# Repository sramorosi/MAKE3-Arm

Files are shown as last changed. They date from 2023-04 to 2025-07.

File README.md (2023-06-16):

# MAKE3-Arm

This repository contains the complete design for the MAKE3 Robot Arm, controller, and the code to control the arm (both remote control and programmable).  This is intended to be a low-cost (less than US $ 250), do it yourself (mostly 3D printed or made with common shop tools), remote controlled robot arm. It can be used for stacking/unstacking things for fun, delivering things without getting too close, as a learning tool whereby you learn by making, and much more.

The design files are in the folder [OpenSCAD-code](/OpenSCAD-code) and are written in [OpenSCAD](https://openscad.org/).  This page contains the **Bill of Materials** for making the MAKE3 Robot Arm, along with notes about what drove the design.

The control code files are in the folder [MAKE3](/MAKE3) and are written in [Arduino C](https://www.arduino.cc/). This page contains information about how the code works and how to calibrate the code for your MAKE3 Robot Arm.
 
## MAKE3 Arm Assembly

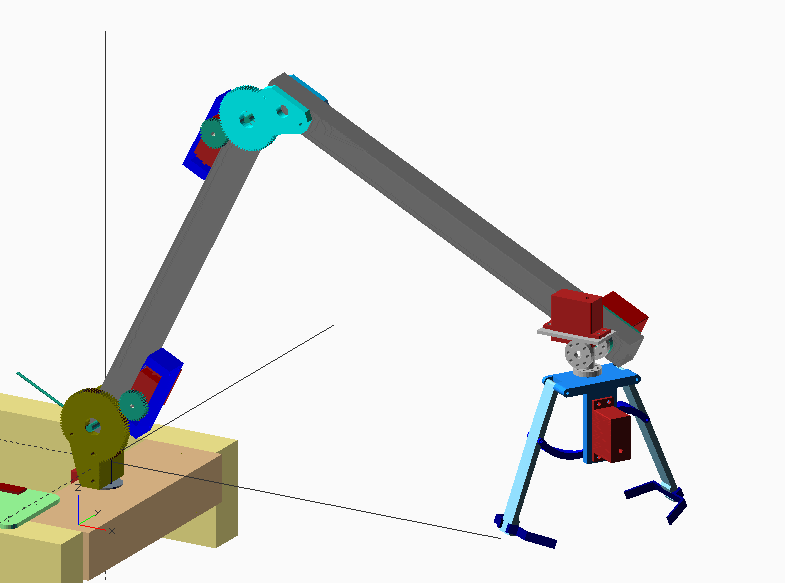
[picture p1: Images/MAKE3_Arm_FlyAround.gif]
MAKE3-Arm-gif

GIF animation of the MAKE3 Robot Arm created in OpenSCAD. 

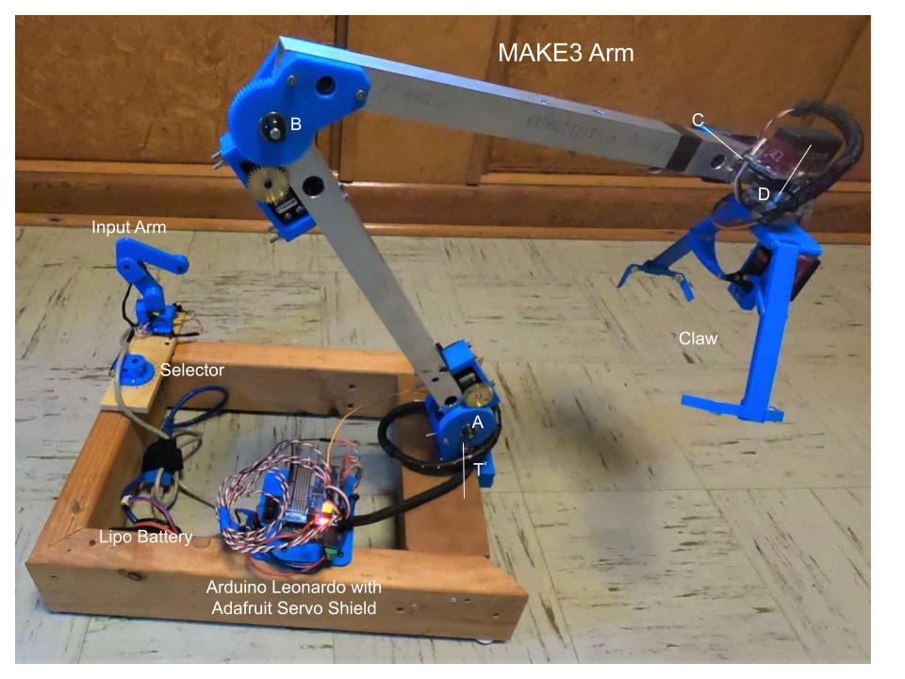
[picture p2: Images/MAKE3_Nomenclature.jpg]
MAKE3 Nomenclature

Labeled photo of the MAKE3 arm.

Video of the MAKE3 robot arm can be found [here](https://youtu.be/0xM0Xhr4jO0)

## MAKE3 Specification

1. The arm has a total reach of about 73 cm. The AB arm is 35 cm and the BC arm is 38 cm
1. The position accuracy at the claw is about plus or minus 0.7 cm. This is based on the angular accuracy of the servos times the gearing and the arm lengths
1. The arm can lift objects up to 200 grams
1. There are no sensors on the MAKE3

## Teaching Objectives

This project is intended as a low cost teaching tool to describe how to design, build and analyze a robot arm.  Some teaching objectives are:

1. Mechanical design of joints (strong, robust, accurate)
1. Principles of Statics (forces and torques/moments)
1. How to create smooth remote control motion
1. How to synchronize control of multiple servos
1. How to make programmed motions fast and smooth
1. How to use trigonometry to get arm angles from a desired point - Inverse Kinematics

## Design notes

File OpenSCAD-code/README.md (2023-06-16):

# OpenSCAD code for MAKE3-Arm

This folder contains the OpenSCAD files that define the MAKE3-Arm and Controllers.

Familiarity with OpenSCAD is required, to make the files for printing and to interogate the design.
 
The OpenSCAD design files are text files that contain the code for the designs.  Use these files to export the .stl files (STL or STereoLithography or Standard Triangle Language) for 3D printing. For more information on how to make .stl files see [making STL models from OpenSCAD](#making-stl-models-from-openscad)

The objective with MAKE3 was to make the design variable-driven (the variables are mostly at the top of each file and should work with the OpenSCAD **Customizer**).

Another objective was to perform some Engineering calculations on the design, using the variables, so one can quickly see if a design will work.

Another objective was to make the 3D printed parts not require supports when printing, to speed up the printing and make accurate parts (small, accurate, fast to print).

Note: OpenSCAD is a Functional Programming Language, and as such one cannot redefine a variable once it has been set.  Most of the code is "simple" programming but for computations involving arrays it becomes more complex.

MAKE3 Nomenclature
Labeled photo of the MAKE3 arm.

The next sections provide the **Bill of Materials** for the MAKE3 arm and control devices, organized by the OpenSCAD files. The files are divided into major assemblies, to keep the files from getting large. There are three major assembly files ([Claw Assembly](#claw_assemblyscad), [Controllers](#controllersscad), and the [MAKE3 Assembly](#make3_assyscad)) and a number of other `include` files that are used with these three main files (`use` is another type of included file in OpenSCAD).   Within the files, there are `modules` or `functions` that break up the code into sub-assemblies, details and other functions.

## MAKE3_Assy.scad

MAKE3-Arm-gif

GIF animation of the MAKE3 Robot Arm created in OpenSCAD. 
[See how to make gifs here](https://github.com/sramorosi/MAKE3-Arm/tree/main/OpenSCAD-code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)

Engineering calculations are performed to find the largest torque on the A, B and C servos.  From these torques a Margin of Safety (MS) calculation is performed to find out if the selected servo will work (that is have a positive MS).  These torques are echoed to the console window, as shown below, and will change as the variables are changed:

```
ECHO: LEN_AB = 350, LEN_BC = 380, LEN_CD = 160, PAYLOAD_MASS = 200
ECHO: BCweight = 259.774, ABweight = 336.371, " grams"
ECHO: "B SERVO MOTOR CAPABILITY=", 250000, " gram-mm"
ECHO: "B Big Gear teeth=", 70, " B_Small Gear teeth =", 32
ECHO: "B GEARED SERVO CAPABILITY=", BGeared_Max_Torque = 546875, " gram-mm"
ECHO: "A SERVO MOTOR CAPABILITY=", 250000, " gram-mm"
ECHO: "A Big Gear teeth=", 80, " ASmall Gear teeth =", 32
ECHO: "A GEARED SERVO CAPABILITY=", AGeared_Max_Torque = 625000, " gram-mm"
ECHO: "A OUTPUT ANGLE=", 144, " DEG"
ECHO: "Turtable Big Gear teeth=", 80, " Turntable Small Gear teeth =", 32
ECHO: "TURNTABLE OUTPUT ANGLE=", 144, " DEG"
ECHO: "C SERVO", " MARGIN OF SAFETY ", MS = 4.20833, max_load = 48000, pos = 4
ECHO: "B SERVO", " MARGIN OF SAFETY ", MS = 1.10963, max_load = 259228, pos = 4
ECHO: "A SERVO - NO SPRING", " MARGIN OF SAFETY ", MS = 0.138404, max_load = 549014, pos = 4
ECHO: A_spr_torque_min = -170310, A_spr_torque_max = 218970
ECHO: "A SERVO - SPRING", " MARGIN OF SAFETY ", MS = 0.797602, max_load = 347685, pos = 9
ECHO: "A SERVO - SPRING - NO PAYLOAD", " MARGIN OF SAFETY ", MS = 2.50475, max_load = -178329, pos = 20
```

The largest moments are *attempted* to be found by performing the calculations on a range of positions, using `function sweep1`. The largest moment values sometime show up at unusual positions. A **static** calculation is performed at each position.  No **dynamic** calculations are performed, and because of this one should have "large" static margins (MS values greater than 0.5 are recommended).

This design has a **torsion spring** located at joint A, which reduces the torque on the A servo.  Above, the fourth line from the bottom shows the margin without a spring (...NO SPRING ... MS = 0.13...) a small or negative MS is BAD.  With a spring MS = 0.79...  I have found that, with a MS less than 0.5, the servos tend to heat up quickly, damaging the servos (I have killed many servos along the way).

Here is the **Bill of Materials**:

### MAKE3_Assy - 3D printed

1. servo_mount (quantity 3), color blue
1. plain_guss (quantity 1), color DeepSkyBlue
1. B_gear_guss (quantity 1), color aqua
1. A_gear_lollypop (quantity 1), gear_side=true, color olive
1. A_gear_lollypop (quantity 1), gear_side=false, color olive
1. turntable_gear (quantity 1), color tomato
1. Electronics_Board (quantity 1), color palegreen

### MAKE3_Assy - Purchased Hardware or other

1. Claw Assembly - See [Claw_Assembly.scad](#claw_assemblyscad)
1. Tube for AB arm: 1" square x 0.065" thick Aluminum tube, 6061 or 6063. This tube is stiff torsionally and the wires can run inside of it. From Online Metals
1. Tube for BC arm: same material as AB arm 
1. Joint A:
    1. Servo, 360 degree, 35 kg-cm torque, FeeTech FT6335M-360, from Amazon
    2. Servo Gear, 32P, 32 Tooth, 25T 3F Spline Servo Mount Gear, from ServoCity
    4. Screws to attach servo to block, Phillips Rounded Head Thread-Forming Screws for Plastic, 18-8 Stainless Steel, Number 4 Size, 1/2" Long, from McMaster Carr
    5. Bearings for main shaft (quantity 2), FR4-ZZ 1/4" x 5/8" x 0.196" Flanged Radial Ball Bearing, from Amazon
    6. Axel, 1/4 inch bolt, or for better precision Rotary Shaft, 303 Stainless Steel, 1/4" Diameter, part no. 1257K115 from McMaster Carr
    1. Set Screw Shaft Collar for 1/4" Diameter (quantity 2), part no. 9414T6 from McMaster Carr 	
    7. Torsion Spring, 90 Degree Left-Hand Wound, 0.848" OD, 0.105" Wire Dia, part no. 9271K589 from McMaster Carr
1. Joint B, same as Joint A, except no spring
1. Joint C:
    1. Servo, 270 degree, 25 kg-cm torque, DS3225MG, from Amazon
    2. Servo Hub (25T Spline), from ServoCity
1. Joint D:
    1. Servo, 270 degree, 25 kg-cm torque, DS3225MG, from Amazon
    2. Standard Hub Shaft Servo Block (25T Spline), from ServoCity
1. Joint T (for turntable):
    1. Servo, 360 degree, 35 kg-cm torque, FeeTech FT6335M-360
    2. Servo Gear (25T Spline), 32 tooth, from ServoCity, same as above
    4. Screws to attach servo to block, same as above
    5. Two Flanged Hex Bore Precision Ball Bearings 1/2” Hex ID x 1-1/8” OD x 5/16” WD, for main shaft, from Amazon
    6. Main Shaft, 1/2" aluminum hex bar, 7075, from Online Metals
1. 2 by 4 wood for base

### MAKE3_Assy - Electronics

Here is the bill of material for the electronics (minus the servos and potentiometers, which are listed with the mechanical assemblies):

1. The microprocessor is an Arduino Leonardo (Note: an Arduino Uno does not work correctly with the Adafruit Servo Shield), from Amazon
1. Adafruit Servo Shield, Shield stacking headers for Arduino (R3 Compatible), 16-Channel 12-bit PWM/Servo Shield - I2C interface
1. Wires from controller to Arduino/Shield. The positive and ground wires can be common for all potentiometers). I have sacrificed CAT-5 Ethernet cable, which have four twisted pairs, or eight wires, so one can wire up to six potentiometers/switches along with the positive and ground wires. All 8 wires have unique colors, which makes it easy to keep track of the wires.
1. Battery - 7.4V Lipo, from Amazon
1. Rocker 2 Position ON-Off Toggle Switch AC 125V/20A, SPST 2 Pins, KCD3-101, from Amazon
1. Misc. connectors for the battery and switch

## Claw_Assembly.scad

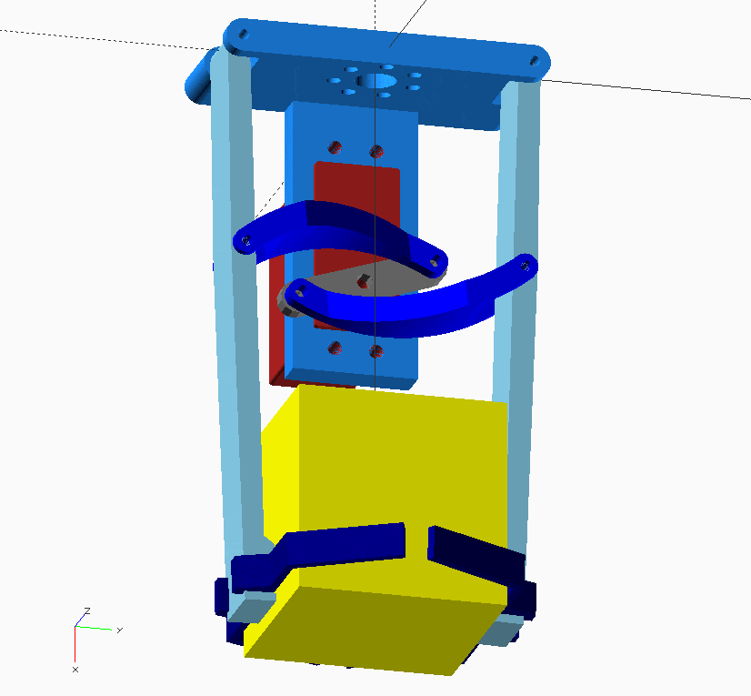
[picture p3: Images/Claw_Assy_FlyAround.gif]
Claw_Assy_FlyAround


This is the claw that attaches to the end of the robot arm. It is designed to be able to pick up items that are roughly 5 to 8 cm in size. The blue curved links are designed to lower the servo torque when the claw is closed, so the servo does not overheat when holding an object. The navy guides are designed to be clipped onto the claw_bars primarily so that 3D printing is faster.

### Claw Parts - 3D printed 

1. curved_link (quantity 2), color blue, supports required. Sometimes called "rod"
2. guide (quantity 2), color navy
3. claw_bar (quantity 2), color SkyBlue
4. base (quantity 1), color DodgerBlue

### Claw Parts - Purchased Parts

1. Servo, 180 degree, 25 kg-cm, DS3225MG, includes horn, horn screws, bushings, from Amazon
2. pins (quantity 4), Spring Steel Slotted Spring Pin, 5/64" Diameter, source McMaster Carr, part number 98296A149
3. screws (quantity 4), attach servo to base, same as for servos on Arm
4. foam window seal, to put on inside of guide for grip

## Controllers.scad

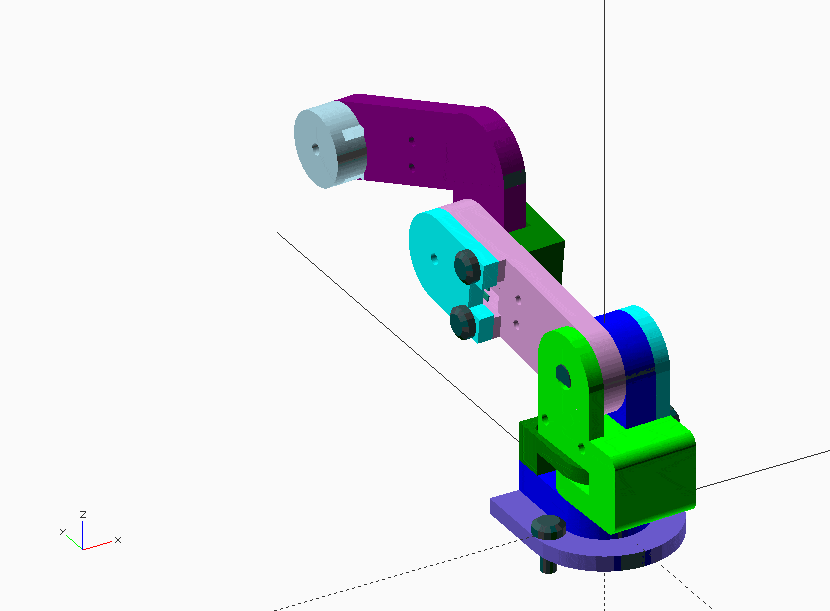
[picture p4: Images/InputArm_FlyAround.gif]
Controller_Arm


This is the *baby* robot arm used to control the big arm. The main design objective was to make the parts 3D printable without supports (for accuracy) so that when assembled the joints have just enough friction so that they move easily but the baby arm will also hold position when it is released.  This design accomplished that!

### Input Arm Controller Parts - 3D printed 

1. PotLug (quantity 2), color blue
2. NonPotLug (quantity 2), color green
3. PotCover (quantity 2), color cyan
4. BasePotCover (quantity 1), color SlateBlue
5. AB_Arm (quantity 1), color plum
6. BC_Arm (quantity 1), color purple
7. BC_Arm_Cap (quantity 1), color lightblue
8. TA_Fitting (quantity 1), color lime

### Input Arm Controller Parts - Purchased Parts

1. Potentiometer (quantity 3), P090L-03F20BR10K, from Mouser Electronics. Snip the extentions off (not the connectors), to fit in the input arm
1. Switch (quantity 1) 12x12x5mm Mini/Micro/Small PCB Momentary Tactile Tact Push Button Switch, from Amazon
1. Screws to hold things together (quantity 9), Phillips Rounded Head Thread-Forming Screws for Plastic, 18-8 Stainless Steel, Number 4 Size, 3/4" Long, from McMaster Carr

## Controllers.scad   (Selector Assembly controller shown)

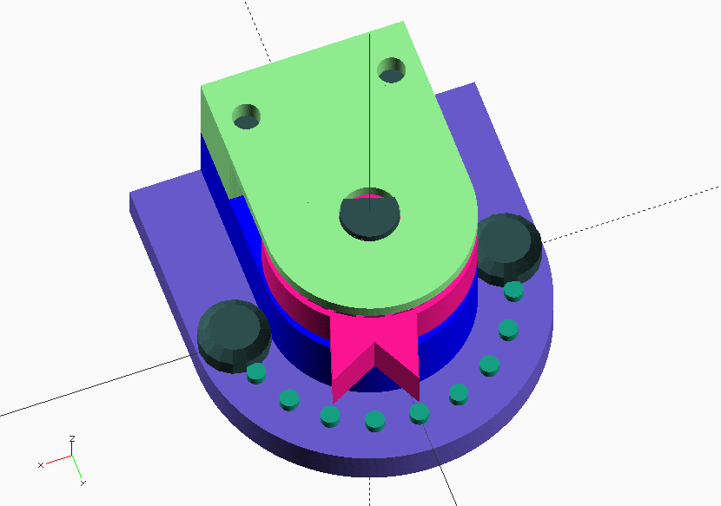
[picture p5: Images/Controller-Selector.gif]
Controller-Selector


### Selector Parts - 3D printed 

1. PotLug (quantity 1), color blue
2. NonPotLugTooth (quantity 1), color lightgreen
3. bumpyBaseCover (quantity 1), color plum
4. SelectorKnot (quantity 1), color DeepPink

### Selector Parts - Purchased Parts

1. Potentiometer (quantity 1), same as used in the input arm above

### Making STL models from OpenSCAD

To make STL models for 3D printing follow these steps for each part that you want to print. The OpenSCAD **Customizer** is handy for changing variables prior to exporting.
1. Toggle off the assembly.  Do not print assemblies.
```OpenSCAD
DISPLAY_ASSY = true;  // set this to false when exporting STL files
```
2. Adjust variables for printing, for example, set FACETS = 140. More facets makes the parts smoother, but takes longer to display.
```OpenSCAD
// use 140 for printing, 40 for display
FACETS = 100; // [40,140]
```
3. Toggle on and off the parts that you want to print by finding the line in the code that draws the part. Remove * (disable) prefix on the line.  Note:  These lines have // EXPORT AS STL at the end of the line.
```
*servo_mount(); // EXPORT AS STL, quantity 2.  remove the * for export
```
4. Render the part **(F6)** Note: Rendering can take much longer than Preview (F5), taking minutes rather than seconds.  Look for a progress bar on the lower right.
5. Export the rendered part as an STL file **(F7)**
6. Load the STL file into your favorite slicer.  Note: Occasionally you may need to perform some STL cleanup, when you detect something not working right in the slicer. I use the 3D Builder tool on Windows for STL repairs.

### Making Animation (.gif or video) files from OpenSCAD

The Animation function **Animate** in OpenSCAD can be toggled on under the **View** menu.

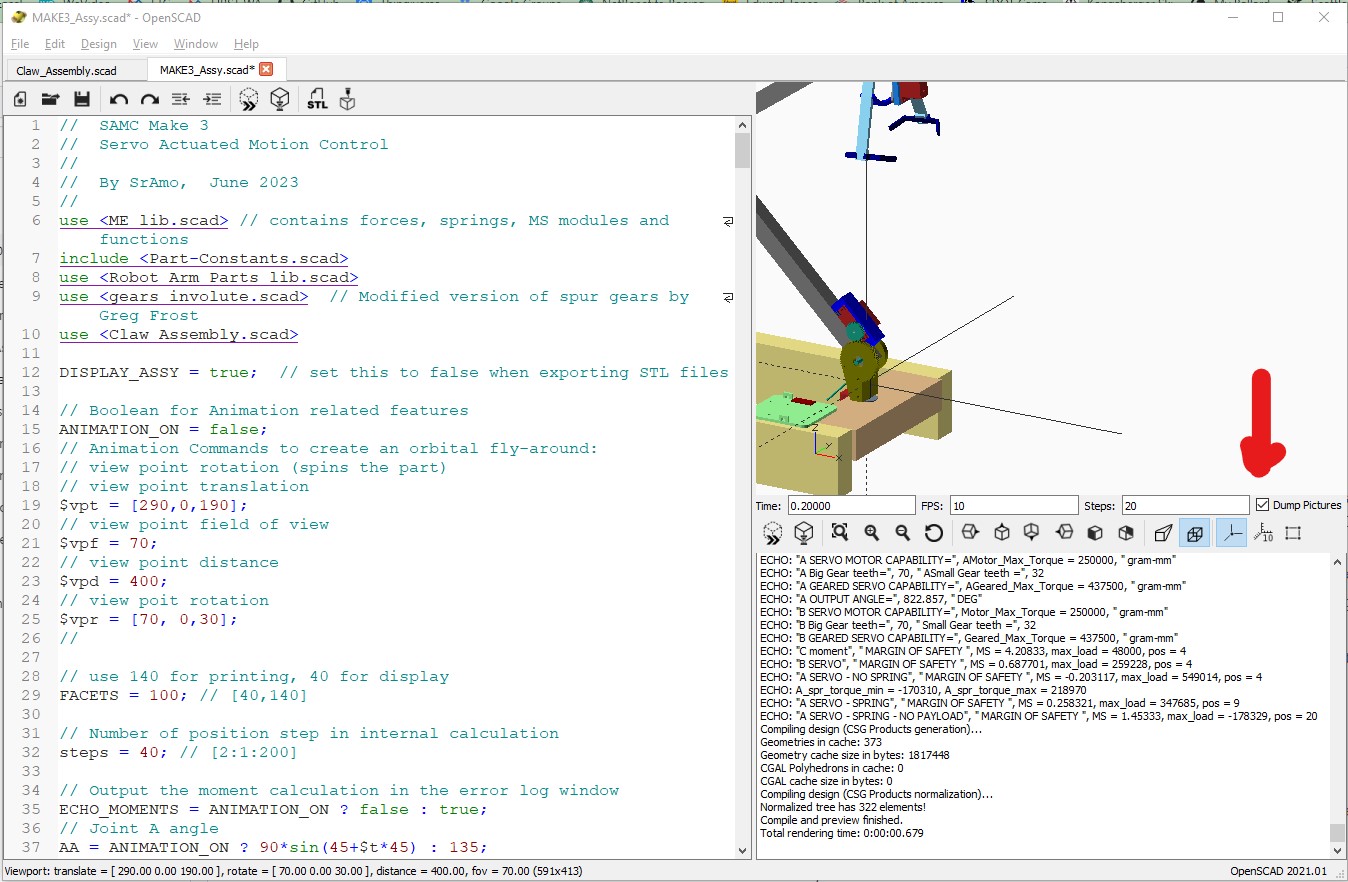
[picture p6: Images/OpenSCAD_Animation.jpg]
MAKE3 Animation Example


While **Animate** is running, enter numbers for FPS and Steps, and check the "Dump Pictures" box just above the console window.  One picture will be created for each frame and saved in the same folder as your OpenSCAD file.

Use the free tool at EZGIF.COM [here](https://ezgif.com/maker) to make a gif or video.  Upload all of the dumped pictures and follow the steps for making a gif.

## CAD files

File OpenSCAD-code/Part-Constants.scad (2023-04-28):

// PART CONSTANT Configuration File
//  last modified October 5 2021 by SrAmo

// conversions
mm_inch = 1/25.4;

// 1/4 ID bearing OD if using a bearing (PART FR4-ZZ C3)
Qtr_bearing_id = 0.25/mm_inch;
Qtr_bearing_od=0.628/mm_inch; // 0.628 inch = 15.9512 mm
Qtr_bearing_flange_od=0.71/mm_inch; // .71 inch = 18.034 mm
Qtr_bearing_flange_t=0.05/mm_inch; // 0.05 inch = 1.27 mm
Qtr_bearing_t=0.155/mm_inch; // 0.155 inch = 3.937 mm

// 1/2 ID flanged bearing 
Half_bearing_id=0.50/mm_inch;
Half_bearing_od=1.125/mm_inch;
Half_bearing_flange_od=1.23/mm_inch; 
Half_bearing_flange_t=0.06/mm_inch; 
Half_bearing_t=0.31/mm_inch; 

M6_bearing_od=12; 
M6_bearing_flange_od=13.6;
M6_bearing_flange_t=0.8;
M6_bearing_t=3.15;

// round belt diameter throughout, if used
//belt_d=4.826;   // 0.19 in = 4.826 mm

hole_qtr_inch=6.48;   // hole for 0.25 inch joint/bolt 0.255 inch = 6.477 mm
hole_no6_screw = 2.5; // hole start diameter for number 6 screw 0.095 inch = 2.413
hole_M3=3.1; // hole for M3 (3 mm) joint/bolt
//hole_M5=5.1;  
hole_M6=6.1;
hole_servo_bushing=3.81; // hole for servo bushing 0.15 inch = 3.81 mm

// STANDARD 40MM X 20MM X 40MM SERVO DIMENSIONS
svo_l = 40.66; // Servo Length for openings in parts
svo_w = 20.3; // Servo Width for openings in parts
svo_d = 42; // Servo Depth from Horn interface to bottom of part
svo_shaft = 10.6; // Servo dist from shaft to edge of body in length direction, was 10.2
svo_screw_l = 49.5; // Servo screw hole length between
svo_screw_w = 10; // Servo screw hole width between
svo_flange_l = 57; // Servo flange length, was 55
svo_flange_t = 3; // Servo flange thickness
svo_flange_d = 10; // Servo depth from Horn interface to top of flange
servo_horn_l=25;
servo_horn_d1=15.25;
servo_horn_d2=7.5;
servo_horn_t=7.4;

// Springs
//  McMaster Carr 9271K619, torsion spring, used in MAKE 2
9271K619_angle = 180; // free leg angle
9271K619_OD = 19.35; // mm
9271K619_wd = 1.9;  // wire diameter mm
9271K619_len = 51;  // arm length mm
9271K619_coils = 7;  // number of coils
9271K619_LH = true;  // LH or RH (false)
9271K619_t = (9271K619_coils+1)*9271K619_wd; // thickness of the spring
9271K619_ID = 9271K619_OD-2*9271K619_wd;  // ID of the coil

//  McMaster Carr 9271K589, torsion spring, used in MAKE 3
9271K589_angle = 90; // free leg angle
9271K589_OD = 21.54; // mm
9271K589_wd = 2.667;  // wire diameter mm
9271K589_len = 88.9;  // arm length mm
9271K589_coils = 5.25;  // number of coils
9271K589_LH = true;  // LH or RH (false)
9271K589_t = (9271K589_coils+1)*9271K589_wd; // thickness of the spring
9271K589_ID = 9271K589_OD-2*9271K589_wd;  // ID of the coil
//9271K589_Dshaft = 12.7; // The largest shaft that can go through spring

pot_shaft_dia = 6.2; // mm, potentiometer shaft dia
pot_lug_t = 8; // thickness of the lug over potentiometer shaft

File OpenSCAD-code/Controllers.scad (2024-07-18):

// Input Control Arm Assembly and Selector Control assembly
//  Design for Human Hand to control a Robot Arm
//  last modified May 2023 by SrAmo
// The parts are designed to not require support material when 3D printing.
//
//  To make STL models for 3D printing follow these steps:
//  find "Export as STL" and remove the * (disable) suffix, 
//     then render the part (F6) (this may take some time)
//        then  Export as STL (F7)
use <ME_lib.scad> // contains forces, springs, MS modules and functions
include <Part-Constants.scad>
use <Robot_Arm_Parts_lib.scad>

/* Animation Commands to create an orbital fly-around:
$vpr = [60, 0, -30];   // view point rotation (spins the part)
$vpt = [-50,0,70];    // view point translation
$vpf = 50;          // view point field of view
$vpd = 150;         // view point distance
*/

// Parameters for Customizer:
// Joint A angle
//AA = 25; // [0:180.0]
AA = 100; //-90*sin($t*180);  // for animation
// Joint B angle
//BB = -35; // [-170:1:0.0]
BB = -50; //90*sin($t*180);  // for animation
// Turntable angle
//TT = 0; // [-90:90]
TT = 60*sin($t*90);  // for animation
// use 140 for printing, 40 for display
FACETS = 100; // [40,140]

// Draw the Input Arm Assembly?
display_assy = true;
// Draw the Selector?
display_selector = false;
// Section cut Assy at X = 0?
clip_yz = false;
// Section cut Assy at Z = 0?
clip_xy = false;

// length of full size A-B arm (mm)
LEN_AB_LARGE=350; 
// length of full size B-C arm (mm)
LEN_BC_LARGE=380; 

// For the Big Arm to move the same as the Small Arm
//  the link lengths should be of consistent scale.
SCALE = 0.15;  // scale of small to big arm

// length of A-B arm, color = plum
lenAB=SCALE*LEN_AB_LARGE;     // mm
// length of B-C arm, color = blue
lenBC=SCALE*LEN_BC_LARGE;      // mm
echo("Baby Arm lengths",SCALE=SCALE,lenAB=lenAB,lenBC=lenBC," mm");

// A joint shift Z (up), mm
A_joint_Z = 34; 
// A joint shift X (lateral), mm
A_joint_X = -9;

// Lug Diameter, mm, used by many
LUG_DIA = 22; 
// distance to the flat side from the bore
FLAT_DIST = 16;
// Main Lug Thickness, mm
MAIN_LUG_THK = 6;
OUTER_LUG_THK = 4;
POT_LUG_THK = 8;
// LUG_Z is the offset for pot removal
LUG_Z = 2;

// Slip fit hole for potentiometer shaft
POT_HOLE_DIA = 6.3; // mm
// McMaster Carr Screw No. 90380A274  to hold lugs together (quantity about 10)
SCREW_DIA = 3.3; // mm, For no. 4 plastic screw, length 0.75 inch

zbody = 5.5;  // Offset for potentiometer body, all units are mm

module screwHoles(dia=15,shrink=false) { // pair of screw holes that hold the stack together
    cylDia = shrink ? SCREW_DIA*0.76 : SCREW_DIA;
    translate([dia/2.8,-dia/2-1,0]) 
        cylinder(h=4*dia,d=cylDia,center=true,$fn=FACETS);
    translate([-dia/2.8,-dia/2-1,0]) 
        cylinder(h=4*dia,d=cylDia,center=true,$fn=FACETS);
}
*rotate([0,0,180]) screwHoles(dia=LUG_DIA);

module ScrewsInHoles(lug_dia=15,screw_dia=4,screw_len=10) { // pair of screws
    // Rounded Head Thread-Forming Screws for Plastic
    translate([lug_dia/2.8,-lug_dia/2-1,0])  Screw(length=screw_len,dia=screw_dia);
    translate([-lug_dia/2.8,-lug_dia/2-1,0]) Screw(length=screw_len,dia=screw_dia);
}

// Full round top, width = dia
module roundTopLug (dia=15,hgt=20,thk=5,bore=3,cyl=false) {  
    difference() {
            hull() {
                translate([0,0,thk/2]) cylinder(h=thk,d=dia,center=true);
                translate([0,-hgt*3/4,thk/2]) cube([dia,hgt/2,thk],center=true);
            }
        cylinder(h=4*thk,d=bore,center=true);  // remove bore
            
        if(cyl) {    
            translate([dia/1.9,-dia/3.1,0]) 
                cylinder(h=hgt*2,d=dia/3.2,center=true,$fn=FACETS);
            translate([-dia/1.9,-dia/3.1,0]) 
                cylinder(h=hgt*2,d=dia/3.2,center=true,$fn=FACETS);
        }
            
    }
}
*roundTopLug(dia=LUG_DIA,hgt=FLAT_DIST,thk=OUTER_LUG_THK,bore=3,$fn=FACETS);  // note result if hgt < dia/2
*roundTopLug(dia=LUG_DIA,hgt=FLAT_DIST,thk=OUTER_LUG_THK,bore=3,cyl=false,$fn=FACETS);

module roundTopLugTwo (width=20,rad=2,hgt=8,thk=5,bore=3) { // Two radius round top
    cylWidth = width/2 - rad;
    difference() {
        translate([0,0,thk/2])
            hull() {
                translate([cylWidth,0,0]) cylinder(h=thk,r=rad,center=true);
                translate([-cylWidth,0,0]) cylinder(h=thk,r=rad,center=true);
                translate([0,-hgt/2,0]) cube([width,hgt,thk],center=true);
            }
        cylinder(h=4*thk,d=bore,center=true);  // remove bore
    }
}
*roundTopLugTwo(bore=0,$fn=FACETS);  // note result if hgt < dia/2

module PotLug(dia=LUG_DIA) {  // Model of Potentiometer holder
    color("blue") difference () {// Side that holds the POT
        roundTopLug(dia=dia,hgt=FLAT_DIST,thk=POT_LUG_THK,bore=POT_HOLE_DIA,$fn=FACETS);

        translate([0,0,zbody]) P090L_pot(negative=true);// remove potentiometer interface

        screwHoles(dia=LUG_DIA);  // remove screw holes
        }
}
*rotate([0,180,0]) PotLug(); // Export as STL... F7 (quantity 2)

module NonPotLug(thk=OUTER_LUG_THK) {  // Model of Potentiometer holder
    color("green") difference() {
            union() {
            translate([0,0,MAIN_LUG_THK]) 
                roundTopLug(dia=LUG_DIA,hgt=FLAT_DIST,thk=thk,bore=POT_HOLE_DIA,$fn=FACETS);
            translate([-LUG_DIA/2,-FLAT_DIST,0]) 
                cube([LUG_DIA,8.5,MAIN_LUG_THK],center=false);
        }
        // remove screw holes
        screwHoles(dia=LUG_DIA,shrink=true);
        
        // remove lug arc from cube
        translate([0,0,-.2]) 
            cylinder(h=MAIN_LUG_THK+.4,d=LUG_DIA*1.03,center=false,$fn=FACETS);
        
        // remove spring wave washer dish
        cylinder(h=MAIN_LUG_THK+.6,d=9.1,center=false,$fn=FACETS);
        
        // remove corner for BC arm motion
        translate([LUG_DIA/2,-LUG_DIA/2,-.2]) rotate([0,0,45])
            cube([6,6,MAIN_LUG_THK+.4],center=false);
    }
}
*rotate([0,180,0]) NonPotLug(); // Export as STL... F7 (quantity 2)

module PotCover() {
    color("cyan") 
    difference () {// Side that holds the POT
        rotate([0,180,0]) 
            translate([0,0,-OUTER_LUG_THK]) 
                roundTopLug(dia=LUG_DIA,hgt=FLAT_DIST,thk=OUTER_LUG_THK,bore=3,cyl=false,$fn=FACETS);
        // Above was cyl=true and trans and rot not required
        // remove potentiometer interface
        translate([0,0,OUTER_LUG_THK+zbody]) P090L_pot(negative=false);
        screwHoles(dia=LUG_DIA);  // remove screw holes
        translate([0,-FLAT_DIST+2,0]) cube([LUG_DIA/2.6,10,10],center=true);
    }
}
*PotCover(); // Export as STL... F7 (quantity 2)

module PotCoverAssy() {
    PotCover();
    ScrewsInHoles(lug_dia=LUG_DIA,screw_dia=4,screw_len=19);
}
*PotCoverAssy();


module joint_visuals(cut=true) { // Use for cross section cuts of Joints
    difference() { 
        union() {
            PotLug(); 
            translate([0,0,zbody]) P090L_pot(negative=false); 
            translate([0,0,POT_LUG_THK]) NonPotLug(); // OR SELECTOR BASE
            translate([0,0,-OUTER_LUG_THK]) PotCoverAssy();
            rotate([0,0,90]) 
                translate([0,0,MAIN_LUG_THK+.2]) 
                    scale([.95,.95,.95]) 
                        AB_Arm(len = lenAB);
       }
       if (cut) translate([-20,0,0]) cube([40,80,40],center=true);  // Section Cut cube
    }
}
*joint_visuals(cut=true); // not for print

module zip_holes() {
    translate([0,3.5,0]) cylinder(h=20,d=2.5,center=true,$fn=36);
    translate([0,-3.5,0]) cylinder(h=20,d=2.5,center=true,$fn=36);
}

module AB_Arm(len=100) {
    color("plum",1) difference () {
        union() {
            translate([0,0,8]) 
                rotate([180,0,-90]) 
                difference() {
                    roundTopLug(dia=LUG_DIA,hgt=FLAT_DIST,thk=MAIN_LUG_THK, bore=3, cyl=true,$fn=FACETS);
                // remove potentiometer interface
                translate([0,0,-LUG_Z]) scale([1.02,1.02,1.02]) rotate([0,0,180]) 
                    P090L_pot(negative=true);
            }
            
            translate([len,0,-0]) 
                rotate([0,0,-90]) PotLug(); // lug at other end
            
            // The connecting cube:
            difference() { // REMOVE CYL SO THAT 0,0 LUG JOINT UNIONS PROPERLY
                translate([LUG_DIA/1.8,-LUG_DIA/2,LUG_Z]) 
                    cube([len-LUG_DIA/.8,LUG_DIA,MAIN_LUG_THK],center=false);
                cylinder(h=40,d=8,center=true,$fn=FACETS); // for the pot
                translate([len/2.6,0,0]) zip_holes();
           }
        }
    }
}
*rotate([180,0,0]) AB_Arm(len = lenAB); // Export as STL... F7 (quantity 1)

module AB_Arm_Assy(len=100){
    AB_Arm(len=len); 
    translate([len,0,0])  rotate([0,0,-90]) {
        translate([0,0,-OUTER_LUG_THK])PotCoverAssy();
        translate([0,0,POT_LUG_THK]) NonPotLug();
    }
    translate([lenAB,0,5]) rotate([0,0,-90]) P090L_pot(negative=false);
}
*AB_Arm_Assy(len=lenAB);
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

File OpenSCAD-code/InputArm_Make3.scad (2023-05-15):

// Input Arm Assembly
//  Design for Human Hand to control a Robot Arm
//  last modified May 2023 by SrAmo
// The parts are designed to not require support material when 3D printing.
//
//  To make STL models for 3D printing follow these steps:
//  find "Export as STL" and remove the * (disable) suffix, 
//     then render the part (F6) (this may take some time)
//        then  Export as STL (F7)
use <ME_lib.scad> // contains forces, springs, MS modules and functions

// Animation Commands to create an orbital fly-around:
$vpr = [60, 0, -30];   // view point rotation (spins the part)
$vpt = [-40,0,80];    // view point translation
$vpf = 50;          // view point field of view
$vpd = 180;         // view point distance
//

// Parameters for Customizer:
// Joint A angle
//AA = 25; // [0:180.0]
AA = 90*sin($t*180);  // for animation
// Joint B angle
//BB = -35; // [-170:1:0.0]
BB = -80*sin($t*90);  // for animation
// Turntable angle
//TT = 0; // [-90:90]
TT = 60*sin($t*90);  // for animation
// use 140 for printing, 40 for display
FACETS = 40; // [40,140]

// Draw the Input Arm Assembly?
display_assy = true;
// Draw the Selector?
display_selector = true;
// Section cut Assy at X = 0?
clip_yz = false;
// Section cut Assy at Z = 0?
clip_xy = false;

// length of full size A-B arm (mm)
LEN_AB_LARGE=350; 
// length of full size B-C arm (mm)
LEN_BC_LARGE=380; 

// For the Big Arm to move the same as the Small Arm
//  the link lengths should be of consistent scale.
SCALE = 0.15;  // scale of small to big arm

// length of A-B arm, color = plum
lenAB=SCALE*LEN_AB_LARGE;     // mm
// length of B-C arm, color = blue
lenBC=SCALE*LEN_BC_LARGE;      // mm
echo("Baby Arm lengths",SCALE=SCALE,lenAB=lenAB,lenBC=lenBC," mm");

// A joint shift Z (up), mm
A_joint_Z = 40; 
// A joint shift X (lateral), mm
A_joint_X = -9;

// Lug Diameter, mm, used by many
LUG_DIA = 22; 
// distance to the flat side from the bore
FLAT_DIST = 20;
// Main Lug Thickness, mm
MAIN_LUG_THK = 6;
OUTER_LUG_THK = 4;
POT_LUG_THK = 8;
// LUG_Z is the offset for pot removal
LUG_Z = 2;

// Slip fit hole for potentiometer shaft
POT_HOLE_DIA = 6.3; // mm
// McMaster Carr Screw No. 90380A274  to hold lugs together (quantity about 10)
SCREW_DIA = 3.3; // mm, For no. 4 plastic screw, length 0.75 inch

//################### PART LIB FUNCTIONS AND MODULES
module washer(d=20,t=2,d_pin=10,center=true){
    // model washer on xy plane at 0,0,0 of diameter d, hole size of d_pin
    // t is thickness
    difference(){
        cylinder(t,d=d,center=center);  // outside
        cylinder(3*t,d=d_pin,center=true);  // subtract bore
    };
}
*washer($fn=FACETS); 

module rounded_cube(size=[20,30,10],r=5,center=true) {
    // Create a rounded cube in the xy plane, flat on the Z ends
    // Creates 4 cylinders and then uses hull
    
    xp=center ? size[0]/2-r : size[0]-r;
    yp=center ? size[1]/2-r : size[1]-r;
    xn=center ? -xp : r;
    yn=center ? -yp : r;
    z=center ? 0 : size[2]/2;

    hull() {
        translate([xp,yp,z]) cylinder(h=size[2],r=r,center=true);
        translate([xp,yn,z]) cylinder(h=size[2],r=r,center=true);
        translate([xn,yp,z]) cylinder(h=size[2],r=r,center=true);
        translate([xn,yn,z]) cylinder(h=size[2],r=r,center=true);       
    }  
}
*rounded_cube(center=false,$fn=FACETS); 

L_pot_shaft = 13.1;  // P090 shaft length above the body (mm)
zbody = 5.5;  // all units are mm

module P090L_pot (negative=false) {
// The P090L (Style L) has the three pins off of the side
// Digi-key part no. P090S-04F20BR10K or P090S-14T20BR10K
// https://www.digikey.com/en/products/detail/tt-electronics-bi/P090S-04F20BR10K/2408853 
// https://www.mouser.com/ProductDetail/BI-Technologies-TT-Electronics/P090S-14T20BR10K
// Solder the wires to the pins (need solid connection). Pins can be easily bent.
// Cut off connectors to reduce installation volume with small diagonal cutters.
// negative false = model a potentiometer for display
// negative true = model to be used with a difference() in another model
    
    ss = negative ? 1.0: 0.97;  // if negative == false then scale down
    // constants
    zbDif = zbody+1;  // make body bigger for difference()

    scale([ss,ss,ss]){ // scale down the model for display
        color("green") if (!negative) { // potentiometer for display
            translate([0,0,-zbody/2]) cube([10,12,zbody],center=true);
            // two cylinders on backside, drawn larger than real
            translate([0,-8.5/2,-zbody]) cylinder(h=4,d=3,center=true,$fn=FACETS);
            translate([0,8.5/2,-zbody]) cylinder(h=4,d=3,center=true,$fn=FACETS);

        } else {         // potentiometer for difference()
            translate([0,0,-zbDif/2]) cube([10,12.5,zbDif],center=true);
            translate([0,-12.5,-zbDif/2]) cube([10,20,zbDif],center=true);
        }
        
        cylinder(h=2,d=7.2,center=true,$fn=FACETS); // ring around the shaft
        
        // two cylinders around the shaft
        translate([2.7,-3.8,0]) cylinder(h=2,d=3,center=true,$fn=FACETS);
        translate([-2.7,3.8,0]) cylinder(h=2,d=3,center=true,$fn=FACETS);
        
    
        // shaft F-Type
        color("darkslategrey") 
            difference () {
                translate([0,0,L_pot_shaft/2]) 
                    cylinder(h=L_pot_shaft,d=6.2,center=true,$fn=FACETS);
                // 1.55 was 1.45, increased to make assembly easier
                translate ([-5,-L_pot_shaft-1.55,5]) cube(L_pot_shaft,center=false); // key
        }
        // pins (3)
        zpin = -4;
        translate([0,-11,zpin]) elect_pin();
        translate([-3,-11,zpin]) elect_pin();
        translate([3,-11,zpin]) elect_pin();
    }
     
    module elect_pin() { // 1 mm diamater electric pin
        cube([1.5,10,0.5],center=true);
    }
}
*P090L_pot(negative=false); 

//######################################################## //
module screwHoles(dia=15,shrink=false) { // pair of screw holes that hold the stack together
    cylDia = shrink ? SCREW_DIA*0.9 : SCREW_DIA;
    translate([dia/2.8,-dia/2-4,0])  cylinder(h=4*dia,d=cylDia,center=true,$fn=FACETS);
    translate([-dia/2.8,-dia/2-4,0]) cylinder(h=4*dia,d=cylDia,center=true,$fn=FACETS);
}
module roundTopLug (dia=15,hgt=20,thk=5,bore=3) {  // Full round top, width = dia
    difference() {
        translate([0,0,thk/2])
            hull() {
                cylinder(h=thk,d=dia,center=true);
                translate([0,-hgt/2,0]) cube([dia,hgt,thk],center=true);
            }
        cylinder(h=4*thk,d=bore,center=true);  // remove bore
    }
}
*roundTopLug(dia=20,hgt=5,bore=0,$fn=FACETS);  // note result if hgt < dia/2

module roundTopLugTwo (width=20,rad=2,hgt=8,thk=5,bore=3) { // Two radius round top
    cylWidth = width/2 - rad;
    difference() {
        translate([0,0,thk/2])
            hull() {
                translate([cylWidth,0,0]) cylinder(h=thk,r=rad,center=true);
                translate([-cylWidth,0,0]) cylinder(h=thk,r=rad,center=true);
                translate([0,-hgt/2,0]) cube([width,hgt,thk],center=true);
            }
        cylinder(h=4*thk,d=bore,center=true);  // remove bore
    }
}
*roundTopLugTwo(bore=0,$fn=FACETS);  // note result if hgt < dia/2

module PotLug() {  // Model of Potentiometer holder
    color("blue") difference () {// Side that holds the POT
        roundTopLug(dia=LUG_DIA,hgt=FLAT_DIST,thk=POT_LUG_THK,bore=POT_HOLE_DIA,$fn=FACETS);

        translate([0,0,zbody]) P090L_pot(negative=true);// remove potentiometer interface

        screwHoles(dia=LUG_DIA);  // remove screw holes
        }
}
*rotate([0,180,0]) PotLug(); // Export as STL... F7 (quantity 4)

module NonPotLug(thk=OUTER_LUG_THK,notch=false) {  // Model of Potentiometer holder
    color("green") difference() {
            union() {
            translate([0,0,MAIN_LUG_THK]) 
                roundTopLug(dia=LUG_DIA,hgt=FLAT_DIST,thk=thk,bore=POT_HOLE_DIA,$fn=FACETS);
            translate([-LUG_DIA/2,-FLAT_DIST,0]) cube([LUG_DIA,8.5,MAIN_LUG_THK],center=false);
            if (notch) translate([0,LUG_DIA/2.2,MAIN_LUG_THK]) rotate([90,0,0])
            linear_extrude(3,convexity=10) polygon(points=[[1.5,0],[0,-1.2],[-1.5,0]]);
        }
        // remove screw holes
        screwHoles(dia=LUG_DIA,shrink=true);
    }
}
*NonPotLug();

module PotCover() {
    color("Cyan") 
    difference () {// Side that holds the POT
        roundTopLug(dia=LUG_DIA,hgt=FLAT_DIST,thk=OUTER_LUG_THK,bore=3,$fn=FACETS);
        // remove potentiometer interface
        translate([0,0,OUTER_LUG_THK+zbody]) P090L_pot(negative=false);
        screwHoles(dia=LUG_DIA);  // remove screw holes
        translate([0,-FLAT_DIST,0]) cube([LUG_DIA/2.6,10,10],center=true);
    }
}
*PotCover(); // STL (2)
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

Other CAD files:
OpenSCAD-code/Robot_Arm_Parts_lib.scad
OpenSCAD-code/Claw_Assembly.scad
OpenSCAD-code/MAKE3_Assy.scad
OpenSCAD-code/ME_lib.scad
OpenSCAD-code/gears_involute.scad

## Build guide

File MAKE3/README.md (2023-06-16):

# Robot Arm Control Code for MAKE3-Arm

This folder contains the Arduino Robot Arm control software for the MAKE3-Arm.

It is written in the C programming language (it does not use C++ objects).  Variables have been grouped into structures using `struct`, to help organize the code.

An understanding of how microcontrollers work is required. Specifically there is an initialization function `setup()` and a repeating `loop()` function. For good robot arm performance it is important to let `loop()` loop as fast as possible. Slow loops can make the arm response jerky and potentially introduce unsteady dynamics. For reference, the MAKE3 runs about 14 milliseconds/loop while in remote control, and about 9 milliseconds/loop while in programmed mode.

The MAKE3 Robot Arm is driven by servos. Servos take **position** command as their input. With the MAKE3, the servo commands are being given (written) every loop!

## Top Level Operation of MAKE3 Arm

There are two basic ways to control the arm. The first is by **remote control** (also called TELEOPERATED), which is the easiest to get working. The second is 
**programmed mode** (also called AUTONOMOUS), which takes more coding and is described further down.

The code is written to control the main arm using the control **Input Arm** and the **Selector**. See folder [OpenSCAD-code](/OpenSCAD-code) for the design of these two control devices.   To avoid using the Selector (recommended for first setup), **add a jumper between analog I/O port 8 and Ground**. This tells the code to stay in TELEOPERATED mode.

The **Input Arm** (or baby arm) is scaled down version of the MAKE3 arm, but it only has joints A, B and T (turntable); it only has potentiometers for these three joints.  The Input Arm also has a **button to control the Claw**, which toggles the claw open and closed.

### Wrist Servos, C and D

The wrist servos, C and D, are always controlled by code (not by an input potentiometer).  In general, the code makes the C servo always point straight down (-90 degrees in global C angle sence). This is done by the function `getCang` shown below.  D is likewise made to **aim** the Claw in a global angle sence. 

```c++
float getCang(float a_angle, float b_angle, float fixed_c_angle) { // returns joint angle C, using A and B
  // Assumes that you want an absolute (fixed) C angle
  return -a_angle - b_angle + fixed_c_angle;
}
```

Having C and D controlled by code makes the arm much easier to operate.

## Calibration of your MAKE3 Arm 

Once a new MAKE3 Robot Arm is completely built, the **first step** is to determine constants for Potentiometers and Servos. These are set in the `setup()` function.
I recommend using a servo tester to get the initial range of motion correct before hooking the servos up the the Arduino/Shield. The calibration involves mapping physical potentiometer angles to millivolt readings and servo angles to microsecond (PWM pulse width) readings.

```c++
void setup() {  // setup code here, to run once:
  // TUNE POTENTIOMETER LOW AND HIGH VALUES
  // FORMAT: initPot(pin,lowmv,lowang,highmv,highang)
  make3.jA.pot = initPot(1 ,905,  0/RADIAN, 112, 180/RADIAN); 
  make3.jB.pot = initPot(5 ,500,-90/RADIAN, 908,  0/RADIAN); 
  make3.jT.pot = initPot(0 ,894, 90/RADIAN, 127, -90.0/RADIAN); 
  jS.pot = initPot(2 , 0, 0/RADIAN, 1023, 280/RADIAN); 

  // TUNE SERVO LOW AND HIGH VALUES
  // FORMAT: initServo(pin,lowang,lowms,highang,highms)
  make3.jA.svo = initServo(0,  7.0/RADIAN, 505, 90.0/RADIAN, 1551);
  make3.jB.svo = initServo(1, 0.0/RADIAN, 500,-175.0/RADIAN, 2320);
  make3.jC.svo = initServo(2, -90.0/RADIAN, 927, 0.0/RADIAN, 1410);
  make3.jD.svo = initServo(3,  -90.0/RADIAN,  811, 90.0/RADIAN, 2054); 
  make3.jCLAW.svo = initServo(4, -45.0/RADIAN,  500, 45.0/RADIAN, 2000); 
  make3.jT.svo = initServo(5,  70.0/RADIAN,  2347, -70.0/RADIAN, 465); 

```

At the end of the main loop there are some telemetry functions (that write values to Serial Output) to help with the callibration:

```c++
  //  Serial Output for Initial Calibration.  One line for each servo.  Turn on one at a time:
  //logData(make3.jA,'A');  // Use logData for Initial Calibration of Potentiometer and Servo A
  //logData(make3.jB,'B');  // Use logData for Initial Calibration of Potentiometer and Servo B
  //logData(make3.jC,'C');  // Use logData for Initial Calibration of Servo C
  //logData(make3.jD,'D');  // Use logData for Initial Calibration of Servo D
  //logData(make3.jT,'T');  // Use logData for Initial Calibration of Potentiometer and Servo T

  // Serial Output  for debugging:
  //logPoint(make3);  // Use for debugging paths
  //logGeneral();  // Use for general debugging
```

## The Main Loop

Here is a **snapshot** of the main loop. The global variable `make3` is a `struct` that organizes the arm data. In the middle of the code the statement `switch (make3.state)` uses the **state** to execute different lines. The state is controlled by the selector. [See section on selector](https://github.com/sramorosi/MAKE3-Arm/tree/main/MAKE3#highest-level-program-control-using-the-selector) 

The TELE state is more complex than one might expect. The TELE method is shown below, in the snapshot of the `loop()`. It is further explained below.

```c++
void loop() {  //########### MAIN LOOP ############
  point angles;  // used in TELEOP by inverseArmKin
  point c_pt;    // used in TELEOP

  stateLoop(make3);  // checks for state change

  loopTime(make3); // Capture cycle time
  
  switch (make3.state) {
    case S_AUTO_2: 
    case S_AUTO_5:
    case S_AUTO_6:
      readCommands(make3,seQ); // read a sequence of commands and act accordingly
      updateJointBySpeed(make3.jCLAW, make3.dt);  // update Claw joint
      break; 
    case S_TELEOP_1: 
    case S_TELEOP_3:
      make3.jA.pot_value = analogRead(make3.jA.pot.analog_pin);  // read joint A
      make3.jB.pot_value = analogRead(make3.jB.pot.analog_pin);  // read joint B
      make3.jT.pot_value = analogRead(make3.jT.pot.analog_pin);  // read the turntable
    
      pot_map(make3.jA);      // get A angle
      pot_map(make3.jB);      // get B angle
      pot_map(make3.jT);      // Get Turntable angle

      make3.target_pt = anglesToG(make3.jA.pot_angle,make3.jB.pot_angle,make3.jT.pot_angle,make3.jC.current_angle,make3.jD.current_angle,LEN_AB,LEN_BC,S_CG_X,S_CG_Y);

      updateArmPtC(make3);   // Move current_pt toward target_pt at given feed rate (mmps)
      c_pt = pointGtoPointC(make3.current_pt,make3.jC.target_angle,make3.jD.target_angle,S_CG_X,S_CG_Y);
      
      inverseArmKin(c_pt,LEN_AB,LEN_BC,angles);    // FIND JOINTS A B T from POINT C
      make3.jA.current_angle = angles.x; //  A 
      make3.jB.current_angle = angles.y;  // local B
      make3.jT.current_angle = angles.z;  //  T
      
      break;
  }
  // Convert the .current_angle(s) to PWM signal and send 
  pwm.writeMicroseconds(make3.jA.svo.digital_pin, servo_map(make3.jA)); // Adafruit servo library
  pwm.writeMicroseconds(make3.jB.svo.digital_pin, servo_map(make3.jB)); // Adafruit servo library
  pwm.writeMicroseconds(make3.jT.svo.digital_pin, servo_map(make3.jT)); // Adafruit servo library
  //
} // END OF MAIN LOOP
```

There are two basic states:
1. The TELE or remote control mode has a number of steps used to make the movements smooth. See the code below the line `case S_TELEOP_3:`  This is the flow:
    1. The potentiometers are read from the input control arm using `analogRead` and mapped to angles using `pot_map`
    2. The point at the end of the arm is calculated from the potentiometer angles using `anglesToG`. This becomes the new target point
    3. The `updateArmPtC` function moves the current point toward the target point in a controlled move.  See [TELE code](https://github.com/sramorosi/MAKE3-Arm/tree/main/MAKE3#tele-remote-control-code-outline)
    4. The joint angles are then solved for the desired current point using the Inverse Kinematics function `inverseArmKin`. 
    5. Finally, the angles are sent to servo to make the arm move using `pwm.writeMicroseconds`.  This is common for both AUTO and TELE (is outside of the switch scope)
1. The AUTO or programmed mode uses function `readCommands` and there is more on that [here](https://github.com/sramorosi/MAKE3-Arm/tree/main/MAKE3#auto-programmable-code-outline)

## TELE (remote control) code outline

The remote control steps were outlined above in the Main Loop discussion. The function that provide smooth remote arm control is `updateArmPtC(arm & the_arm)` The function has three main features that provide the control: 

1. There is a linear velocity limit `feedRate` on the movement of the end of the arm. This is implemented in the function updateArmPtC shown below.  The code keeps track of the Current C point, and when the user moves the control arm, a new Target C point is calculated.  The function limits how fast the arm can move from current to target. This prevents rapid movement of the arm when it is extended, which is when the most damage could occur.

2. The velocity is further decrease when the distance from current to target point is < RAMP_START_DIST (~50 mm), using this formula:  `newFeedRate = the_arm.feedRate * (the_arm.line_len/RAMP_START_DIST); `  This helps with the fine movements when picking and placing.

3. To prevent a bad rocking dynamic when the arm is pointed close to straight up, the velocity is further decreased.  This is done by looking at the 2D (xy plane) current-target point distance, and if it is close (<100 mm) to 0,0 then `Vnew = Vmax x ((dist + 50) / 150)`. 

Here is a **snapshot** of updateArmPtC:

```c++
void updateArmPtC(arm & the_arm) { // Moves current point C toward target_pt at given feed rate (mm/sec)
  float moveDist,newFeedRate,distC;
  the_arm.line_len = ptpt_dist(the_arm.current_pt,the_arm.target_pt);
  // cut the feedrate when the current pt x,y component is close to zero.  To stop the rocking dynamics. 
  distC = sqrt(pow(the_arm.current_pt.x,2)+pow(the_arm.current_pt.y,2));
  newFeedRate = the_arm.feedRate;
    if (distC < 100) newFeedRate = newFeedRate*((distC+50)/150);  // Ramp down math
    if (the_arm.line_len < RAMP_START_DIST) {
      newFeedRate = the_arm.feedRate*(the_arm.line_len/RAMP_START_DIST);  // scale down based on distance
    } else {
      newFeedRate = the_arm.feedRate;  // keep using the current feedrate
    };
  moveDist = newFeedRate/1000.0 * (the_arm.dt); // dist(mm) = feed rate(mm/ms)*dt(ms)  
  the_arm.current_pt = pt_on_line(moveDist,the_arm.line_len, the_arm.current_pt,the_arm.target_pt);
}
```

## Highest level program control, using the Selector

The Selector lets you pick one of multiple different programs for the arm

Controller-Selector

There are two main modes by which one can control the Arm:

1. Remote Control (teleoperated or TELE) using the Control Arm
2. Programmably (autonomously or AUTO) using command sequences within the code

The different program modes (TELE or AUTO) are chosen using the Selector and are called **states**, which are defined by constants in the code. The following code block shows a few of the state constants.

```c++
// STATES (or programs)  Controlled by the selector potentiometer.
#define S_TELEOP_1 1   
#define S_AUTO_2   2 
#define S_TELEOP_3 3 
```
## AUTO (programmable) code outline

The autonomous **Programming Commands** are defined by constants. These commands are shown below:

```c++
// Synchronous commands (completes command before next command is sent) -- see runCommand
#define K_TIMER 1    // timer {milliseconds}
#define K_LINE_G 3   // line move to new G point {feed rate, x,y,z}     PATH METHOD
#define K_ORBIT_Z 4  // G point circular orbit  {feed rate, x-center(mm),radius(mm),angle_sweep(deg)}
                     //  angle_sweep should be between 90 and 270. Motion will be CCW.  If negative, motion will be CW 
// Asynchronous commands (does not wait to be completed)
#define K_AIM 5     // Turns on AIM mode. The aiming point is the parameters {x,y,z}
#define K_LIFT 6    // Turns on or off the z-lift mode for the K_LINE_G command.  parameters = {0=off, 1=on;  z-lift amount(mm)}
#define K_GOTO 9    // Go back to given command line {command line number} 
#define K_COMBINE 10 // combines given x y z values with an existing command
#define K_CLAW 11   // claw local move      {angle rate, target angle}
#define K_END 99   // indicates to stop running commands
```

Here is a **snapshot** of `readCommands`. At the moment, there is a global 2D array of fixed length `seQ` that holds commands.

```c++
#define SIZE_CMD_ARRAY 5  // NUMBER OF VARIABLES PER COMMAND 
struct command {int arg[SIZE_CMD_ARRAY];};

struct sequence {  // An array of commands
  int nuHm_cmds;
  command cmd[];  // undefined array length
};

sequence seQ = {4,{{0,0,0,0,0},
                {0,0,0,0,0}, 
                {0,0,0,0,0},
                {0,0,0,0,0}}}; 

void readCommands(arm & the_arm, sequence & the_seq) {  // read through commands
  if (the_arm.n > the_seq.nuHm_cmds || the_arm.n >= 999) {  // DONE RUNNING ARRAY OF COMMANDS
    return;  
  } else {
    if (runCommand(the_arm, the_seq, the_arm.n)) { // true = done = go to the next command
      the_arm.n = the_arm.n + 1; // go to the next command line
      the_arm.line_len = 0.0;    // initialize line length
      the_arm.timerStart = millis();  // for timed commands
    };
    return;
  };
}
```

## Example AUTO Program

Programs are initialized when the loop sees a new state that is an AUTO state. The initialization is done in the function `stateLoop(arm & the_arm)` Below is a **snapshot** from stateloop of a program to move to a point and get ready pick up something.  This is the method by which one programs the arm.

```c++
      case S_AUTO_5:  // PREPARE FOR FIRST BLOCK GRAB
        the_arm.n = 0; // reset command pointer
        the_arm.loopCount = 0;
        the_arm.mode = HM_CD_AIM;   // K_LINE does not set aim mode
        make3.aim_pt.x = 250; make3.aim_pt.y =-5000; make3.aim_pt.z = 100;
        setCmd(seQ.cmd[0],K_LIFT,0,0,0,0);          // turn lift off
        setCmd(seQ.cmd[1],K_LINE_G,300,250,200,-50);  // move to start
        setCmd(seQ.cmd[2],K_CLAW,  200,-15,500,0); // open claw and wait
        setCmd(seQ.cmd[3],K_END,0,0,0,0); 
        break;      
```

### How K_LINE_G works in AUTO

The K_LINE_G command moves the arm grabber point **G** from one point to another point along a linear path, usually.  There is an option to **lift** the arm between the points. The function `path_line` **builds an array of robot arm angles**, on the fly, that will move the arm smoothly from start to end point. Here is a snapshot of the code:

```c++
void path_line(pathAngles & the_pathA,point start,point end, point aim,boolean liftMiddle,int lift) {  
  // Build a G-point path from start to end, and aligns D-angle to aim at point aim
  // Path increments (equivalent to velocity) are sized by a sine wave from 0 to 180 deg, to minimize accelerations
  // ASSUMES THAT THE C JOINT IS -90 DEG ABSOLUTE (POINTING DOWN)
  //   since c joint is rotated -90, then S_CG_X is added to z 
  // ASSUMES THAT S_CG_Z IS ZERO (G POINT IS ALONG AXIS OF D SERVO)
  // If boolean liftMiddle == true then function (zLift = cos(a)*lift) is added to c.z 
  int i;  
  point angles;  // used to receive angles from IK
  point c,g;
  float g_dist, cg_vect_ang, d_aim_angle,lineLen,travel,a,angIncrement;

  lineLen = ptpt_dist(start,end);  // 3d distance from point start to end
  travel = 0.0;  // initialize travel
  angIncrement = (180.0/RADIAN)/(PATH_SIZE-1);  // set angle increment
  a = -90.0/RADIAN;   // initialize SINE WAVE FUNCTION
  for(i=0;i<PATH_SIZE;++i) {
    travel = (sin(a)+1.0)*lineLen/2.0;  // distance traveled, SINE WAVE FUNCTION
    g = pt_on_line(travel,lineLen,start,end);

    g_dist = ptpt_dist({0,0,0},{g.x,g.y,0});  // g distance from origin, xy only
    cg_vect_ang = asin(g.y/g_dist) + asin(-S_CG_Y/g_dist) + 90.0/RADIAN;  // TRICKY TRIG HERE
    c.x = g.x - S_CG_Y*cos(cg_vect_ang); // account for the S_CG_Y offset in both x and y
    c.y = g.y - S_CG_Y*sin(cg_vect_ang);   

    if (liftMiddle) c.z = g.z + S_CG_X + cos(a)*lift;  // add the lift function
    else c.z = g.z + S_CG_X;        // don't add the lift function (straight line path)

    inverseArmKin(c,LEN_AB,LEN_BC,angles); // feed c to the inverse function
    the_pathA.a[i] = angles.x*ANGLE_SCALE;   // SCALE RADIANS AND STORE AS INTEGER
    //the_pathA.a[i] = a*ANGLE_SCALE;   // SCALE RADIANS AND STORE AS INTEGER
    the_pathA.b[i] = angles.y*ANGLE_SCALE;
    the_pathA.c[i] = getCang(angles.x,angles.y,-90.0/RADIAN)*ANGLE_SCALE;
    // USE AIM POINT TO FIND D ANGLE
    d_aim_angle = atan2((aim.y-g.y),(aim.x-g.x));
    the_pathA.d[i] = (angles.z - d_aim_angle)*ANGLE_SCALE;
    the_pathA.t[i] = angles.z*ANGLE_SCALE; 

    a = a + angIncrement;
  }
}
```

K_ORBIT works in a similar method to K_LINE_G, except that the path on the xy plane is an arc, and the aiming of the claw is toward the arc center.

## Inverse Kinematics Function, used in TELE and AUTO

The code for the Inverse Kinematincs function is shown here:

```c++
void inverseArmKin(point c, float l_ab, float l_bc,point & angles) {
  // Given robot arm Ground-Turtable-AB-BC, where Turntable and A are [0,0,0]
  // The location of joint C (point c) and the lengths AB (l_ab) and BC (l_bc) are specified
  // The joints A,B are on a turntable with rotation T parallel to Z through A
  // With T_angle = 0, then joints A & B are parallel to the Y axis
  // Calculate the angles given pt C ***Inverse Kinematics***
  // returns an array (TYPE point) with [A_angle,B_angle,T_angle] in radians
  //
  // Inverse Kinematics is not much more than a few tri formulas
  // A Reference to the math is here: https://appliedgo.net/roboticarm/
  //
  float c_len, sub_angle1, sub_angle2;
  point c_new;
  static float tAngMemory = 0.0;  //  NEEDS TO BE STATIC

  // Check for near negative x values to prevent bad math, arm clashes
  if (c.x < 2.0) {  // 2 mm
    c.x = 2.0;
    angles.z = tAngMemory/1.3;  // ease the transition toward zero turntable angle
  } else {
    angles.z = atan2(c.y,c.x);   // turntable angle, compute with pos x
  }
  tAngMemory = angles.z;

  // CONVERT THE 3D POINT PROBLEM TO A 2D PROBLEM, FOR SOLVING THE INVESE KINEMATICS
  c_new = rot_pt_z(c,-angles.z); // rotate the point c onto the XZ plane using turntable angle
  c_len = sqrt(pow((c_new.x),2)+pow(c_new.z,2));   // XZ plane, reuse variable c_len

  // THIS IS THE 2D INVESE KINEMATIC MATH
  if (c_len < l_ab+l_bc) {
    // case where robot arm can reach
    sub_angle1 = atan2(c_new.z,c_new.x);
    sub_angle2 = acos((pow(c_len,2)+pow(l_ab,2)-pow(l_bc,2))/(2*c_len*l_ab));
    angles.x = sub_angle1 + sub_angle2;
    angles.y = acos((pow(l_bc,2)+pow(l_ab,2)-pow(c_len,2))/(2*l_bc*l_ab))-180.0/RADIAN;
  } else {
    // case where robot arm can not reach point... 
    angles.x = atan2(c_new.z,c_new.x); // a angle point in direction to go
    angles.y = 0.0; // b is straight
  } 
}
```

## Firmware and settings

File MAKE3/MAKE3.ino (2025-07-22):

/* ROBOT ARM CONTROL SOFTWARE FOR MAKE3 ROBOT ARM
 *  By, SrAmo, May 2023
 *  Written for an Arduino Leonardo and an Adafruit Servo Shield.
 */
#include <Adafruit_PWMServoDriver.h>

#define SERVO_FREQ 50 // Analog servos run at ~50 Hz updates, from Adafruit
#define RADIAN 57.2957795  // number of degrees in one radian
#define RAMP_START_DIST 50 // distance at which velocity ramp-down begins (mm) used in velocity control
#define ZERO_DIST 0.5     // value used to determine if distance is zero (mm)

// STATES (or programs)  Controlled by the selector potentiometer
//#define S_SERIAL 0      // enter a serial command from serial.input
#define S_TELEOP_1 1   
#define S_AUTO_2   2 
#define S_TELEOP_3 3 
#define S_TELEOP_4 4
#define S_AUTO_5 5   // wait above block
#define S_AUTO_6 6   // block stack sequence
#define S_AUTO_7 7   // block to block stack sequence
#define S_TELEOP_8 8   
#define S_TELEOP_9 9  
#define S_AUTO_10 10 

// HAND MODES control how the end of the arm can operate (joints C and D)
// Note: For each loop the arm C point is obtained (from multiple methods) and angles A, B and T are solved (inverse kinematics)
#define HM_CD_LOC 0
#define HM_CD_ABS 1
#define HM_C_LOC_D_ABS 2
#define HM_C_ABS_D_LOC 3
#define HM_CD_AIM 4
#define HM_NONE 5  // No Hand Mode is applied

/*
 *  COMMAND CODES: All codes are integers
 *  Feed rate is in mm per second.
 *  Angle rate is in Degrees per second.
 *  Angles given in Degrees.  Locations in mm.
 */
#define SIZE_CMD_ARRAY 5  // NUMBER OF VARIABLES PER COMMAND. 

// Synchronous commands (completes command before next command is sent) -- see runCommand
#define K_TIMER 1    // timer {milliseconds}
#define K_LINE_G 3   // line move to new G point {feed rate, x,y,z}     PATH METHOD
#define K_ORBIT_Z 4  // G point circular orbit  {feed rate, x-center(mm),radius(mm),angle_sweep(deg)}
                     //  angle_sweep should be between 90 and 270. Motion will be CCW.  If negative, motion will be CW 
// Asynchronous commands (does not wait to be completed)
#define K_AIM 5     // Turns on AIM mode. The aiming point is the parameters {x,y,z}
#define K_LIFT 6    // Turns on or off the z-lift mode for the K_LINE_G command.  parameters = {0=off, 1=on;  z-lift amount(mm)}
#define K_GOTO 9    // Go back to given command line {command line number} 
#define K_COMBINE 10 // combines given x y z values with an existing command
#define K_CLAW 11   // claw local move      {angle rate, target angle}
#define K_END 99   // indicates to stop running commands
//#define K_C_LOC 12    // C local move           {angle rate, target angle}
//#define K_C_ABS 13    // C Absolute Angle Mode, {angle rate, target angle}
//#define K_D_LOC 14    // D local move           {angle rate, target angle}
//#define K_D_ABS 15     // D Absolute Angle Mode {angle rate, target angle}

// GEOMETRY OF ARM:
#define LEN_AB 350.0     // Length of Input AB arm in mm
#define LEN_BC 380.0     // Length of Input BC arm in mm
#define FLOOR -140.0     // Distance from A joint to Floor in mm (-140 mm claw, -50 with camera)
#define S_CG_X 150.0    // offset from joint C to G in X.  180 is a claw value,  90 is GoPro
#define S_CG_Y -38.0     // offset from joint C to G in Y.  -38 is GoPro
#define S_CG_Z 0.0     // offset from joint C to G in Z.  40 is Claw.  0 is GoPro
 /*  STRUCTURES FOR MATH, SERVOS, POTENTIOMETERS, JOINTS, and ARM  */
struct point {float x,y,z;}; 
struct line {struct point p1 , p2; };

struct potentiometer {
  int analog_pin; // Arduino analog pin number (0 - 5)
  int low_mv; // low voltage value, from 0 (0 Volts) to 1023 (5 Volts)
  float low_ang; // corresponding angle at low voltage, in radians
  int high_mv; // high voltage value, from 0 (0 Volts) to 1023 (5 Volts)
  float high_ang; // corresponding angle at high voltage, in radians
  // Note: low and high values do not need to be  at the extreems
  //  Tip:  Pick low and high angles that are easy to read/set/measure
  //      Values outside of the low and high will be extrapolated
};

struct servo {
  // Values are pulse width in microseconds (~400 to ~2400--SERVOS SHOULD BE TESTED)
  // 270 deg servo, gets 290 deg motion with 400 to 2500 microsecond range
  // 180 deg servo, gets 160 deg motion with 500 to 2800 microsecond range
  uint8_t digital_pin; // Adafruit digital pin number
  int low_ms; // low microsecond value, from about 500 to 2400
  float low_ang; // corresponding angle at low microsecond, in radians
  int high_ms; // high microsecond value, from about 500 to 2400
  float high_ang; // corresponding angle at high microsecond, in radians
}; 

struct joint {
  potentiometer pot; // Sub structure which contains static pot information
  servo svo; // Sub structure which contains the static servo information
  int pot_value;  // current potentiometer value in millivolts
  float pot_angle; // Potentiometer arm angle, if used, in radians
  float current_angle; // last issued command for angl, in radians
  float target_angle;  // where the angle should end up, in radians
  float target_velocity;  // radians per millisecond
};

struct digiSwitchStruct {  // structure for physical button switch connected to a digital input pin
  int inputPin = 5;
  boolean isOn = false;  // each time the button is pushed the value is toggled
  int delayMS = 500;     // delay time to avoid switch bounce, in milliseconds
  unsigned long timerStart; // timer variable for the delay, se we don't use delay() in loop
};


struct arm {  // as in Robot Arm
  int state; // The different ways that the arm can be controlled. Set by S potentiometer
  int mode; // The mode in which the arm runs, primarily the end effector (C and D joints)
  int n; // current active index in the command array
  int loopCount;  // for command looping (using K_GOTO), this keeps track of the loop number  
  boolean initialize;  //  for initializing commands
  unsigned long prior_mst; // clock time (microseconds) prior loop 
  unsigned long dt; // delta loop time in ms
  unsigned long timerStart; // timer, for delays
  float feedRate; // feed rate for point moves, in mm/sec (converted to /microsec)
  point current_pt; // current (C or G) point 
  point target_pt;  // target C or G point
  point aim_pt;   // aiming point 
  float line_len;  // calculated distance from current_pt to target_pt
  joint jA;
  joint jB;
  joint jC;
  joint jD;
  joint jCLAW;
  joint jT;
};

struct command {unsigned long arg[SIZE_CMD_ARRAY];}; // was int

struct sequence {  // An array of commands
  int nuHm_cmds;
  command cmd[];  // undefined array length
};

// Path of Servo Angles.  Stored as integer to minimize memory usage.  Scale by at least 1000 for smooth results
#define PATH_SIZE 20   // was 20
#define ANGLE_SCALE 1000   // used to store radians in integer format (radian*SCALE)
struct pathAngles {
  int a[PATH_SIZE];
  int b[PATH_SIZE];
  int c[PATH_SIZE];
  int d[PATH_SIZE];
  int t[PATH_SIZE];        
};

//   GOBAL VARIABLES 
arm make3; 
joint jS;  // selector pot
digiSwitchStruct clawSwitch;  // holds data for the claw push button switch
pathAngles pathA; // for storing pre-computed servo angles

sequence seQ = {2,{{0,0,0,0,0},
//                {0,0,0,0,0}, 
//                {0,0,0,0,0},
//                {0,0,0,0,0},
//                {0,0,0,0,0},
//                {0,0,0,0,0},
//                {0,0,0,0,0},
//                {0,0,0,0,0},
//                {0,0,0,0,0},
//                {0,0,0,0,0},
//                {0,0,0,0,0},
                {0,0,0,0,0}}}; 
                           
// called this way, it uses the default address 0x40
Adafruit_PWMServoDriver pwm = Adafruit_PWMServoDriver();

// SETTERS,  INITIALIZERS
potentiometer initPot(int pin, int lowmv, float lowang, int highmv, float highang) {
  // initPot(pin,lowmv,lowang,highmv,highang)
  // Note: low and high values do not need to be  at the extreems
  struct potentiometer pot;
  pot.analog_pin = pin;
  pot.low_mv = lowmv;
  pot.low_ang = lowang;
  pot.high_mv = highmv;
  pot.high_ang = highang;
  return pot;
}

servo initServo(int pin, float lowang, int lowms, float highang, int highms) {
  // initServo(pin,lowang,lowms,highang,highmv)
  // Note: low and high values do not need to be  at the extreems
  struct servo svo;
  svo.digital_pin = pin;
  svo.low_ang = lowang;
  svo.low_ms = lowms;
  svo.high_ang = highang;
  svo.high_ms = highms;
  return svo;
}

void initJoint(joint & jt, float initial_angle) {
  // Sets initial joint values
  // Note: can't read physical servo angle, so servos can jump on startup
  jt.current_angle = initial_angle;
  jt.target_angle = initial_angle;
  jt.target_velocity = 60.0/RADIAN/1000.0;  // default initial velocity, radians per microsecond
}

void initArm(arm & the_arm, point pt) { // starting point for arm
  // initialize arm structure
  the_arm.state = 0;
  the_arm.mode = HM_CD_ABS;  
  the_arm.n = -1;  // first command, USE -1 TO INDICATE NOT RUNNING A COMMAND
  the_arm.loopCount = 0;
  the_arm.initialize = true;  
  the_arm.prior_mst = millis();
  the_arm.dt = 10;  
  the_arm.timerStart = millis();
  the_arm.feedRate = 250.0;  
  the_arm.current_pt = pt;
  the_arm.target_pt = pt;
  the_arm.aim_pt = pt;
  the_arm.aim_pt.x = the_arm.aim_pt.x + 300.0;
  the_arm.line_len = 0.0;
}

void initSwitch(digiSwitchStruct & theSwitch,int pin, int delay) {
  theSwitch.inputPin = pin;
  theSwitch.isOn = false;
  theSwitch.delayMS = delay;
  theSwitch.timerStart = 0;
}

void checkSwitch(digiSwitchStruct & theSwitch) { // checks if the switch has been pressed and sets isOn variable
  int reading = digitalRead(theSwitch.inputPin);
  int deltaTime = millis() - theSwitch.timerStart;
  if ((reading == 0) && (deltaTime > theSwitch.delayMS)) { // check is switch has toggled
    theSwitch.isOn = !theSwitch.isOn;
    theSwitch.timerStart = millis(); // timer is done, reset
  }
}

float getCang(float a_angle, float b_angle, float fixed_c_angle) { // returns joint angle C, using A and B
  // Assumes that you want an absolute (fixed) C angle
  return -a_angle - b_angle + fixed_c_angle;
}

//  ###############  MATH FUNCTIONS ###########################
float floatMap(float x, float in_min, float in_max, float out_min, float out_max) {
  return (x - in_min) * (out_max - out_min) / (in_max - in_min) + out_min;
}

point rot_pt_x(point p1, float a) { // Rotate p1 about X axis by a radians
  point p2;
  p2.x = p1.x;
  p2.y = p1.y*cos(a)-p1.z*sin(a);
  p2.z = p1.y*sin(a)+p1.z*cos(a);
  return p2;
}

point rot_pt_y(point p1, float a) { // Rotate p1 about Y axis by a radians
  point p2;
  p2.x = p1.x*cos(a)-p1.z*sin(a);
  p2.y = p1.y;
  p2.z = p1.x*sin(a)+p1.z*cos(a);
  return p2;
}

point rot_pt_z(point p1, float a) { // Rotate p1 about Z axis by a radians
  point p2;
  p2.x = p1.x*cos(a)-p1.y*sin(a);
  p2.y = p1.x*sin(a)+p1.y*cos(a);
  p2.z = p1.z;
  return p2;
}

point add_pts(point p1, point p2) {
  point p3;
  p3.x = p1.x+p2.x;   p3.y = p1.y+p2.y;   p3.z = p1.z+p2.z;
  return p3;
}
float ptpt_dist(point p1, point p2) {
  return  sqrt(pow(p1.x-p2.x,2.0)+pow(p1.y-p2.y,2.0)+pow(p1.z-p2.z,2.0) );
}

point pt_on_line(float s, float dist, point p1, point p2) { // point along line s from p1
  point new_pt;
  float ratio;
  ratio = s / dist; 
  new_pt.x = ratio*(p2.x-p1.x) + p1.x;
  new_pt.y = ratio*(p2.y-p1.y) + p1.y;
  new_pt.z = ratio*(p2.z-p1.z) + p1.z;
  return new_pt;
}

void inverseArmKin(point c, float l_ab, float l_bc, point & angles) {
  // Given robot arm Ground-Turtable-AB-BC, where Turntable and A are [0,0,0]
  // The location of joint C (point c) and the lengths AB (l_ab) and BC (l_bc) are specified
  // The joints A,B are on a turntable with rotation T parallel to Z through A
  // With T_angle = 0, then joints A & B are parallel to the Y axis
  // Calculate the angles given pt C ***Inverse Kinematics***
  // RETURNS angles (array of TYPE point) with [A_angle,B_angle,T_angle] in radians
  //
  // Inverse Kinematics is a few trig formulas
  // A Reference to the math is here: https://appliedgo.net/roboticarm/
  //
  float c_len, sub_angle1, sub_angle2;
  point c_new;
  static float tAngMemory = 0.0;  //  NEEDS TO BE STATIC

  // Check for near negative x values to prevent bad math, arm clashes
  if (c.x < 2.0) {  // 2 mm
    c.x = 2.0;
    angles.z = tAngMemory/1.3;  // ease the transition toward zero turntable angle
  } else {
    angles.z = atan2(c.y,c.x);   // turntable angle, compute with pos x
  }
  tAngMemory = angles.z;

  // CONVERT 3D POINT TO A 2D POINT, FOR SOLVING THE INVESE KINEMATICS
  c_new = rot_pt_z(c,-angles.z); // rotate the point c onto the XZ plane using turntable angle
  c_len = sqrt(pow((c_new.x),2)+pow(c_new.z,2));   // XZ plane, reuse variable c_len

  // THIS IS THE 2D INVESE KINEMATIC MATH
  if (c_len < l_ab+l_bc) {
    // case where robot arm can reach
    sub_angle1 = atan2(c_new.z,c_new.x);
    sub_angle2 = acos((pow(c_len,2)+pow(l_ab,2)-pow(l_bc,2))/(2*c_len*l_ab));
    angles.x = sub_angle1 + sub_angle2;
    angles.y = acos((pow(l_bc,2)+pow(l_ab,2)-pow(c_len,2))/(2*l_bc*l_ab))-180.0/RADIAN;
  } else {
    // case where robot arm can not reach point... 
    angles.x = atan2(c_new.z,c_new.x); // a angle point in direction to go
    angles.y = 0.0; // b is straight
  } 
}

void inverseArmKin2D(point c, float l_ab, float l_bc, point & angles) {
  // Given robot arm Ground-Turtable-AB-BC, where Turntable and A are [0,0,0]
  // The location of joint C (point c) and the lengths AB (l_ab) and BC (l_bc) are specified
  // The joints A,B are on a turntable with rotation T parallel to Z through A
  // With T_angle = 0, then joints A & B are parallel to the Y axis
  // Calculate the angles given pt C ***Inverse Kinematics***
  // RETURNS angles (array of TYPE point) with [A_angle,B_angle,0] in radians
  //
  // Inverse Kinematics is a few trig formulas
  // A Reference to the math is here: https://appliedgo.net/roboticarm/
  //
  float c_len, sub_angle1, sub_angle2;

  angles.z = 0.0;  // 2D, this is always zero

  c_len = sqrt(pow((c.x),2)+pow(c.z,2));   // XZ plane
  // Check for near zero values to prevent bad math, arm clashes
  if (c_len < 2.0) {  // 2 mm
    c.x = 2.0;
    c_len = 2.0;
  } 

  // THIS IS THE 2D INVESE KINEMATIC MATH
  if (c_len < l_ab+l_bc) {
    // case where robot arm can reach
    sub_angle1 = atan2(c.z,c.x);
    sub_angle2 = acos((pow(c_len,2)+pow(l_ab,2)-pow(l_bc,2))/(2*c_len*l_ab));
    angles.x = sub_angle1 + sub_angle2;
    angles.y = acos((pow(l_bc,2)+pow(l_ab,2)-pow(c_len,2))/(2*l_bc*l_ab))-180.0/RADIAN;
  } else {
    // case where robot arm can not reach point... 
    angles.x = atan2(c.z,c.x); // a angle point in direction to go
    angles.y = 0.0; // b is straight
  } 
}

/*
point anglesToC(float a, float b, float t, float l_ab, float l_bc){  // Forward Kinematics
  // Apply translations and rotations to get the C point
  point pB,pC, pTemp;
  pB.x = l_ab;   pB.y = 0.0;  pB.z = 0.0;
  pC.x = l_bc;   pC.y = 0.0;  pC.z = 0.0;
  pTemp = rot_pt_y(pC,b);  // rotate b
  pC = add_pts(pB,pTemp);  // add to AB arm
  pTemp = rot_pt_y(pC,a); // rotate a
  pC = rot_pt_z(pTemp,t);  // rotate turntable
  return pC;
}  */

//  Forward Kinematics, Apply translations and rotations to get point G
//  Used by Teleoperated only
point anglesToG(float a, float b, float t, float c, float d, float l_ab, float l_bc, float sCGx, float sCGy) {
  point pB,pC, pG, pTemp;
  
  pB.x = l_ab;   pB.y = 0.0;  pB.z = 0.0;
  pC.x = l_bc;   pC.y = 0.0;  pC.z = 0.0;
  pG.x = sCGx;   pG.y = sCGy;  pG.z = 0.0;

  pTemp = rot_pt_x(pG,d);  // rotate point G about d
  pG = rot_pt_y(pTemp,c);  // rotate c
  pTemp = add_pts(pC,pG);  // add G to BC arm
  pG = rot_pt_y(pTemp,b);  // rotate b
  pTemp = add_pts(pB,pG);     // add to AB arm
  pG = rot_pt_y(pTemp,a); // rotate a
  pTemp = rot_pt_z(pG,t);  // rotate turntable
  return pTemp;
}  
point pointGtoPointC(point pG,float c, float d, float sCGx, float sCGy) {
  point plocalG,pTemp;  
  plocalG.x = -sCGx;   plocalG.y = -sCGy;  plocalG.z = 0.0;
  pTemp = rot_pt_x(plocalG,d);  // rotate point G about d
  plocalG = rot_pt_y(pTemp,c);  // rotate c
  pTemp = add_pts(plocalG,pG);  // add 
  return pTemp;  
}
void pot_map(joint & jt) { // Map a potentiometer value in millivolts to an angle
  // map(value, fromLow, fromHigh, toLow, toHigh), USES INTEGER MATH
  // NOTE: SCALE ANGLES (RADIANS) UP THEN DOWN TO GET PRECISION FROM POT VALUES
  jt.pot_angle = map(jt.pot_value, jt.pot.low_mv, jt.pot.high_mv, jt.pot.low_ang*1000, jt.pot.high_ang*1000) / 1000.0; 
  jt.target_angle = jt.pot_angle;  // assume that the two are equal for now, RADIANS
}

float servo_map(joint & jt) { // Map current joint angle to the servo microsecond value
  return floatMap(jt.current_angle, jt.svo.low_ang, jt.svo.high_ang, jt.svo.low_ms, jt.svo.high_ms);
}

// Move Current toward Target at given RateLimit (no units)
// Used in Teleoperated only
float rateLimitMove(float Target, float Current, float RateLimit) { 
  float delta, newV=0;
  delta = Target-Current;
  if (abs(delta) > abs(RateLimit)) { // rate limit the move
      if (delta > 0 ) { 
        newV = Current + abs(RateLimit);  
      } else if (delta < 0)  {
        newV = Current - abs(RateLimit);  
      };
  } else {
    newV = Current + delta;
  }
  return newV;
}
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
void loop() {  //########### MAIN LOOP ############
  //static command cmd = {0,0,0,0,0};  // used in Serial Read
  //static boolean runningCmd = false; // toggle for serial read
  point angles;  // used by inverseArmKin
  point c_pt;

  stateLoop(make3);  // checks for state change

  loopTime(make3); // Capture cycle time
  
  switch (make3.state) {
    case S_AUTO_2: 
    case S_AUTO_5:
    case S_AUTO_6:
    case S_AUTO_7:
      readCommands(make3,seQ); // read a sequence of commands and act accordingly
      updateJointBySpeed(make3.jCLAW, make3.dt);  // update Claw joint
      break; 
    case S_TELEOP_1: 
    case S_TELEOP_3:
    case S_TELEOP_4: 
    case S_TELEOP_8:
    case S_TELEOP_9:
      make3.jA.pot_value = analogRead(make3.jA.pot.analog_pin);  // read joint A
      make3.jB.pot_value = analogRead(make3.jB.pot.analog_pin);  // read joint B
      //make3.jD.pot_value = analogRead(make3.jD.pot.analog_pin);  // read D wrist
      make3.jT.pot_value = analogRead(make3.jT.pot.analog_pin);  // read the turntable
      //make3.jCLAW.pot_value = analogRead(make3.jCLAW.pot.analog_pin);  // read joint Claw
    
      pot_map(make3.jA);      // get A angle
      pot_map(make3.jB);      // get B angle
      //pot_map(make3.jD);      // Wrist
      pot_map(make3.jT);      // Get Turntable angle
      //pot_map(make3.jCLAW);   // get Claw angle

      checkSwitch(clawSwitch);
      if (clawSwitch.isOn) make3.jCLAW.current_angle = 45.0/RADIAN;
      else make3.jCLAW.current_angle = -10.0/RADIAN;
      make3.jCLAW.target_angle = make3.jCLAW.current_angle; // for Claw, target should always equal current

      // Convert Input Arm angles to Robot Arm Point G (gripper)
      // UPDATE:  removed the Turntable Angle, (set it to always be zero)
      make3.target_pt = anglesToG(make3.jA.pot_angle , make3.jB.pot_angle, 0.0 , make3.jC.current_angle , make3.jD.current_angle , LEN_AB , LEN_BC , S_CG_X , S_CG_Y);

      // Move current point C toward target_pt at given feed rate (mm/sec)
      updateArmPtC(make3);   
      c_pt = pointGtoPointC(make3.current_pt,make3.jC.target_angle,make3.jD.target_angle,S_CG_X,S_CG_Y);
      
      // FIND JOINTS A B T from POINT C
      // UPDATE:  Make 2D version, without Turntable
      inverseArmKin2D(c_pt,LEN_AB,LEN_BC,angles);    
      make3.jA.current_angle = angles.x; //  A 
      make3.jB.current_angle = angles.y;  // local B

      // UPDATE: SET DIRECT TO POT ANGLE??? OR MAKE SMOOTH UPDATE METHOD
      make3.jT.current_angle = rateLimitMove(make3.jT.pot_angle , make3.jT.current_angle , 0.006); // angles.z;  //  T
      
      loopUpdateWrist(make3);  // HAND JOINT UPDATE 
      updateJointBySpeed(make3.jC, make3.dt);  
      updateJointBySpeed(make3.jD, make3.dt);  

      // HARD LIMIT to keeps the claw from contacting BC arm
      if (make3.current_pt.z > (LEN_AB) ) make3.jC.target_angle = (-90.0+ 45.0*(make3.current_pt.z-(LEN_AB))/(LEN_BC-40))/RADIAN; 
      else make3.jC.target_angle = -90.0/RADIAN;

      break;
    default:  // unspecified state should do nothing
      break;
  }

  // FLOOR HARD LIMITS
  if (make3.current_pt.z < (FLOOR+15) ) make3.current_pt.z = FLOOR+15;  // this keeps the arm from doing a pushup
  
  //  Serial Output for Initial Calibration.  One line for each servo.  Turn on one at a time:
  //logData(make3.jA,'A');  // Use logData for Initial Calibration of Potentiometer and Servo A
  //logData(make3.jB,'B');  // Use logData for Initial Calibration of Potentiometer and Servo B
  //logData(make3.jC,'C');  // Use logData for Initial Calibration of Servo C
  //logData(make3.jD,'D');  // Use logData for Initial Calibration of Servo D
  //logData(make3.jT,'T');  // Use logData for Initial Calibration of Potentiometer and Servo T

  // Serial Output  for debugging:
  //logPoint(make3);  // Use for debugging paths
  logGeneral();  // Use for general debugging

  blink();  // blinks the led on the arduino board

  // Convert the .current_angle(s) to PWM signal and send 
  pwm.writeMicroseconds(make3.jA.svo.digital_pin, servo_map(make3.jA)); // Adafruit servo library
  pwm.writeMicroseconds(make3.jB.svo.digital_pin, servo_map(make3.jB)); // Adafruit servo library
  pwm.writeMicroseconds(make3.jC.svo.digital_pin, servo_map(make3.jC)); // Adafruit servo library
  pwm.writeMicroseconds(make3.jD.svo.digital_pin, servo_map(make3.jD)); // Adafruit servo library
  pwm.writeMicroseconds(make3.jCLAW.svo.digital_pin, servo_map(make3.jCLAW)); // Adafruit servo library
  pwm.writeMicroseconds(make3.jT.svo.digital_pin, servo_map(make3.jT)); // Adafruit servo library
  //
} // END OF MAIN LOOP

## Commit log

2023-04-28 Add InputArm
    [InputArm_Make3.scad]
2023-04-28 Add all OpenSCAD files
    [Claw_Assembly.scad, InputArm_Make3.scad, MAKE3_Assy.scad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]
2023-04-28 ME_lib update
    [ME_lib.scad]
2023-05-06 Make3 Input Arm mostly complete
    [InputArm_Make3.scad, ME_lib.scad]
2023-05-12 Add Claw Assy GIF
    [Claw_Assembly.scad, InputArm_Make3.scad, Robot_Arm_Parts_lib.scad]
2023-05-15 Better GIFs
    [InputArm_Make3.scad, MAKE3_Assy.scad]
2023-05-16 Add selector image
    [Claw_Assembly.scad]
2023-05-16 Claw updates
    [Claw_Assembly.scad]
2023-05-21 More documentation updates
    [Claw_Assembly.scad, Controllers.scad, MAKE3_Assy.scad]
2023-05-25 Documentation Updates
    [Claw_Assembly.scad, Controllers.scad]
2023-06-01 README updates
    [Claw_Assembly.scad, MAKE3_Assy.scad]
2023-06-08 Mostly README updates
    [Controllers.scad, MAKE3_Assy.scad]
2023-06-09 GIF updates and more
    [Controllers.scad, Robot_Arm_Parts_lib.scad]
2023-06-16 Small updates
    [Claw_Assembly.scad, Controllers.scad, Robot_Arm_Parts_lib.scad]
2023-08-21 minor lib updates
    [ME_lib.scad, Robot_Arm_Parts_lib.scad]
2024-03-06 In Teleop, remove Turntable from Inverse calculation (fix bug)
    [Robot_Arm_Parts_lib.scad]
2024-07-03 Minor Claw Updates
    [Claw_Assembly.scad, Controllers.scad, ME_lib.scad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]
2024-07-16 baby arm update
    [Claw_Assembly.scad, Controllers.scad, Robot_Arm_Parts_lib.scad]
2024-07-18 New arm base
    [Controllers.scad, MAKE3_Assy.scad]
2024-07-22 small arduino code tune
2025-07-22 save stuff from may 2025
    [MAKE3_Assy.scad, ME_lib.scad]
2025-07-22 minor button investigation
2025-07-31 Minor claw changes
    [Claw_Assembly.scad]
